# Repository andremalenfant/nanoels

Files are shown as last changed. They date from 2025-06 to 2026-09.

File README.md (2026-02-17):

Fork including:

- Touch Screen
- Upload Screen & ESP firmware from the web page
- Yellow background (a tribute to H4's design) in h5-2axis-yellow.HMI.
- Included HMI files are configured for the Nextion Enhanced 3.2" screen as it's the biggest that would fit my lathe head.
- Encoder to replace 0-9 and + - Enter, etc. to gain screen real estate (because of the smaller screen)

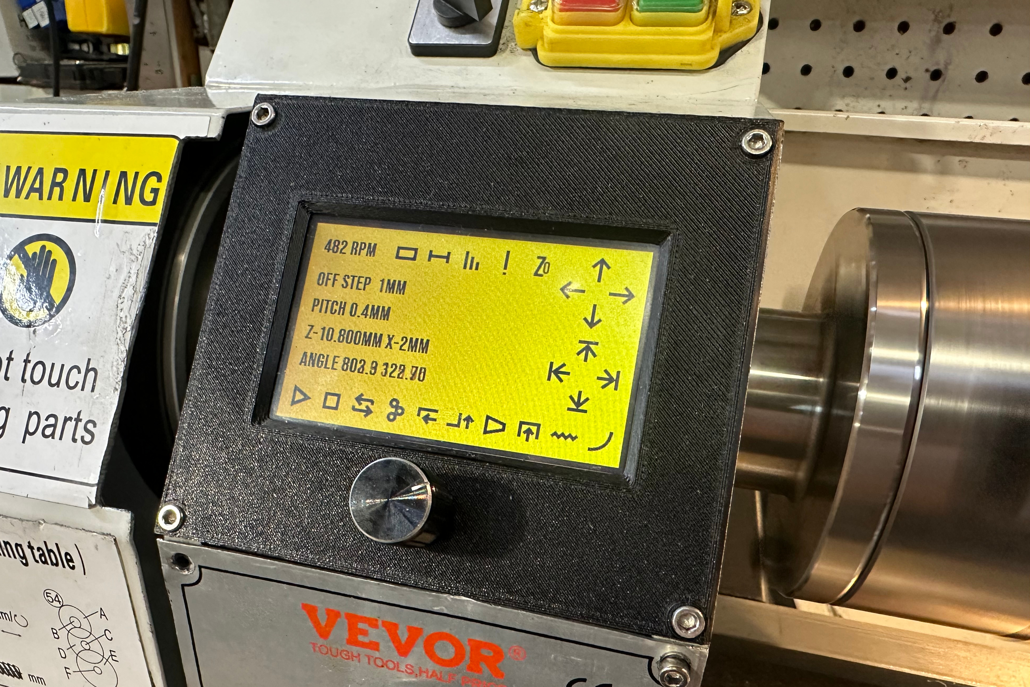
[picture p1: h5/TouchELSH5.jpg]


This software and instructions are [provided as is](LICENSE), without warranty of any kind. [🇷🇺 Перевод на русский](https://translate.google.com/translate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), [🇩🇪 deutsche Übersetzung](https://translate.google.com/translate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)

# NanoEls H5

CNC and electronic lead screw controller based on ESP32-S3 that supports up to 3 axes:

- All the features of H4
- Cheaper and much easier to make than H4
- External PS2 keyboard
- High resolution touch screen
- More ports: joystick, MPGs, scales



See [h5 folder for hardware files, software and assembly](https://github.com/kachurovskiy/nanoels/tree/main/h5).

# NanoEls H4

CNC and electronic lead screw controller based on ESP32-S3 that supports up to 4 axes:

- Automatic threads including multi-start
- Multi-pass turning, facing and cones
- Precise movements, soft limits and much more

h4-600px

See [h4 folder for hardware files, software, assembly and usage manual](https://github.com/kachurovskiy/nanoels/tree/main/h4).

## Build examples

- [fmw626](https://github.com/kachurovskiy/nanoels/discussions/123)
- [Kissys](https://github.com/kachurovskiy/nanoels/discussions/121)

# NanoEls H2

Cheap DIY Electronic Lead Screw (ELS) based on Arduino Nano for metal lathes. No more greasy gear swapping! Control your metal lathe lead screw with a few clicks.

- Set leadscrew pitch for feed or thread
- Soft limits for the carriage
- Multi-start threads in 1 start of the spindle



See [h2 folder for parts list, software, assembly and usage manual](https://github.com/kachurovskiy/nanoels/blob/main/h2/). Controller can be built from [generally available components](https://github.com/kachurovskiy/nanoels/tree/main/h2#components).

It's suggested to use STEPPERONLINE CL57T closed-loop driver with NEMA 23 3NM motor or stronger with 200 step resolution mode (full step) and a 600 PPR optical rotary encoder. [See hardware.md for more info.](hardware.md)

## Build examples

- [EdFleta](https://github.com/kachurovskiy/nanoels/discussions/87)
- [fmw626](https://github.com/kachurovskiy/nanoels/discussions/118)
- [Johannmupa](https://github.com/kachurovskiy/nanoels/discussions/89)
- [kachurovskiy](https://youtu.be/jR4tBBHSl3c?t=62)

# Contributing to the project

- Questions, problems and improvements: please start [a new GitHub Discussion](https://github.com/kachurovskiy/nanoels/discussions/new) or a new Issue
- Successful builds: please start a new GitHub Discussion with photos and comments

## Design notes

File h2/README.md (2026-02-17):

This software and instructions are provided as is, [without warranty of any kind](LICENSE).

# NanoEls H2

This is the second hardware version (hence H2) of NanoEls electronic lead screw controller. It still uses Arduino Nano
microcontroller, a [custom PCB board](https://github.com/kachurovskiy/nanoels/blob/main/h2/Gerber_PCB_NanoElsLcd_20220815.zip) you
can print cheaply on jlcpcb.com and a few widely available components allowing you to build a DIY single-axis ELS.



Features:

- Big screen
- Nice terminals
- Convenient buttons
- Disabling stepper when it's not used (less buzzing)
- Controlling left/right movement step - 1mm, 0.1mm, 0.01mm and 0.001mm
- Higher precision when turning imperial pitches
- Moving left/right while ON
- On/off switch
- Tachometer
- Multi-start threads
- Asynchronous mode
- Metric, inch and TPI support
- Quick reverse

⚠️ Due to Arduino relatively low frequency and realtime requirements (can't plan the motion ahead) H2 can only issue 2800 step impulses per second. This means that the motor can reach ~800 RPM at 200 steps per revolution or ~200 RPM at 800 steps per revolution. Make sure to use a motor with a driver that can do full steps or use the [H5 controller](https://github.com/kachurovskiy/nanoels/tree/main/h5) instead.

## Components

- Arduino Nano (mini USB style)
- 2004 LCD display
- 12 buttons 6x6mm, each 6mm tall
- 8 1kOhm resistors, one 1MOhm resistor (or similar)
- 6 M3 nylon stand-offs (12mm long) and screws
- 3 KF2EDG sockets (Curved needle, 4P, 3.5MM)
- 3 KF2EDG plugs (Plug Terminal, 4P, 3.5MM)
- MTS-102 on-off switch
- RV09 10kOhm potentiometer
- 6 M3 threaded inserts

All of this can easily be found on AliExpress, eBay or Amazon.

## Case

3D models ready for printing: [main case](https://github.com/kachurovskiy/nanoels/blob/main/h2/nanoels-lcd-case.stl),
[lid](https://github.com/kachurovskiy/nanoels/blob/main/h2/nanoels-lcd-lid.stl),
[button](https://github.com/kachurovskiy/nanoels/blob/main/h2/nanoels-lcd-button.stl). You can print it at home or e.g. at [JLCPCB](https://cart.jlcpcb.com/quote).

## Assembly

1. Check that your Arduino Nano is functional before soldering
1. Solder everything except the display onto the PCB, pay attention which side a part should be facing (up/down/left/right) and ensure Arduino pins won't be touching the display later
1. Ensure perfect soldering joints on 1kOhm resistors or the vertical row of buttons won't work well
1. Solder the display
1. Check that your board is working (connect to a PC via Arduino Nano USB port, upload code) before inserting it into the case
1. Push threaded inserts into the case using your soldering iron
1. Drill out the main case button holes using a 7mm drill and ensure the buttons are moving freely
1. Insert buttons into the case, insert PCB, screw in stand-offs (sorry, it's non-trivial), close the lid and screw it to the stand-offs

## Wiring

Starting from the top terminal:

- 5V - connect to 5V power supply positive output (usually red) through an emergency stop button
- GND - connect to 5V power supply negative output (usually black)

Encoder terminal:

- ENCA - connect to one of the encoder signal lines
- ENCB - connect to one of the encoder signal lines
- 5V - connect to encoder power-in line (usually red)
- GND - connect to encoder power-in line (usually black) and wire shielding if there's any

Stepper terminal:

- STEP - connect to stepper driver PUL-
- DIR - connect to stepper driver DIR-
- ENA - connect to stepper driver ENA-
- 5V - connect to stepper driver PUL+, DIR+, ENA+ and wire shielding if there's any

## Schematics

**WARNING:** trying to build this on a breadboard will result in [interference problems](https://github.com/kachurovskiy/nanoels/discussions/89) and will likely make the device unusable. Please use the PCB instead.



## PCB



[Gerber ZIP](https://github.com/kachurovskiy/nanoels/blob/main/h2/Gerber_PCB_NanoElsLcd_20220815.zip)

## Programming the Arduino

- Download the Arduino IDE
- Install `LiquidCrystal` and `FastGPIO` libraries via the Library Manager in the Arduino IDE
- Download [this repository](https://github.com/kachurovskiy/nanoels/archive/refs/heads/main.zip), unzip, go to `h2` directory and open `h2.ino` file in Arduino IDE
- Check the top constants (e.g. encoder steps, motor steps, display offset) and adjust if needed
- Upload the sketch to your Arduino Nano
- Spindle direction: show angle on screen using top-right button. Rotate the chuck forward manually - angle should increase. If it decreases, swap `ENC_A` and `ENC_B` values in the code, re-upload the sketch
- Motor direction: try `LEFT` and `RIGHT` buttons - if motor is moving in the wrong direction, change the value of `INVERT_STEPPER` in the code, re-upload the sketch

# Operating the ELS



## Safety

- **In case of unexpected movements use Emergency Stop button.** Ensure that your Emergency Stop button stops all motion and it can't automatically restart when Emergency Stop is lifted.
- Ensure that your machine complies with all applicable laws and regulations e.g. [Machinery Directive](https://eur-lex.europa.eu/legal-content/EN/TXT/?uri=celex%3A32006L0042) in Europe.
- Test the controller functionality before relying on it. Don't operate machinery without the necessary training and knowledge, in a hurry or when tired.

## Switching between metric and imperial

Use button that is second from the bottom in the vertical row of buttons to change the system of measurement between:

- Metric (mm)
- Inch
- TPI

It affects how the pitch and position is displayed and changes, move steps for precision moves.

## Setting pitch

Pitch is the distance that carriage will move when the spindle makes the full turn. For example, M14 thread uses 2mm pitch.

Select the desired pitch using `-` and `+` buttons. If you keep the buttons pressed, the pitch starts changing faster after a few seconds.

Use negative pitch values e.g. `-2mm` to cut left-to-right threads. Do do that, you have 2 options:

- hold the `-` button until the pitch drops below 0 to the required value
- or press the bottom-right button to toggle the pitch sign between `+` and `-`

Some inch threads require setting the micron part (3rd precision point) of the pitch, to do that click the `Step` button until you're in the `0.001mm` mode. Now clicking `-` or `+` buttons will change the pitch by a micron.

## Turning

- Set desired pitch using `-` and `+` buttons
- Turn on the lead screw using the `ON` button
- Start the lathe spindle, use `LEFT` and `RIGHT` buttons to move if needed, stop spindle when done
- Turn off the lead screw using the `ON` button

## Soft limits / automatic stops

Move the carriage using `LEFT` or `RIGHT` to the desired stop position and press `L STOP` or `R STOP` depending on which limit you'd like to set.

When both limits are set, you can:

- Use lathe forward/reverse spindle movements to move the carriage between the stops
- Use `LEFT` and `RIGHT` buttons to move the carriage within the stops

Setting only one stop is also supported. Stops aren't lost when `ON` button is clicked or pitch is changed.

## Moving the carriage

Use `LEFT` and `RIGHT` buttons to move the carriage. If stops are set, they will be respected during the movement.

When the ELS is off, carriage will move by the distance set using `Step` button but at least 1 stepper motor step.

When the ELS is ON, carriage will move in pitch increments (stay in the thread) and travel at least the distance set by `Step` button.

## Multi-start threads

Use middle button in the right-side vertical row of buttons (`Mode` button) and switch into the `MUL` mode. Use `+` and `-` buttons to increase/decrease the number of starts in your multi-start thread.

Set left and right limits. Cut thread normally and use `LEFT` or `RIGHT` buttons to move the carriage between cuts (no need to turn off the spindle). Controller automatically moves to the next start of the thread when a limit is reached.

## Asynchronous mode

Click `Mode` button until you enter the `ASY` mode. In this mode the spindle rotation is ignored and motor moves with a constant speed of 1 pitch per second when ELS is `ON`. Limits and manual movement works normally.

## Losing the thread

The spindle and stepper positions are reset to 0 `ON`, `-` or `+` buttons are pressed.

## Out-of-sync situations

It's possible for the lead screw to go out of sync with the spindle by removing the `L STOP` or `R STOP` while the carriage is standing on it. It's indicated by the `SYN` word on the display.

This situation should resolve itself once the spindle makes a full turn.

## Resetting ELS and viewing the software version

ELS remembers all the positions and ON/OFF status when powered off. Hold `ON` button for 5+ seconds to:

  - Reset stepper and spindle positions to 0
  - Resets pitch to 0
  - Removes stops
  - Removes out-of-sync state
  - Shows NanoEls version

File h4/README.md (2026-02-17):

# NanoEls H4

4-axis Electronic Lead Screw (ELS) based on ESP32-S3 for metal lathes.

h4-600px

Controller is no longer available for purchase on https://kachurovskiy.com/ but you can DIY with the hardware design files provided.

## Features

- Metric, inch and TPI support, cut any thread with utmost precision
- Controls 2 axes - lead screw (Z) and cross-slide (X)
- Manual movement of both axes: by eye, in precise steps or by a precise amount
- Disabling/enabling of stepper motors allowing to switch to manual operations in 1 click
- Soft limits allowing to cut e.g. close to the chuck
- Automatic threads: just set length, depth, pitch and number of passes
- Automatic multi-pass turning and facing
- Automatic multi-start threads
- Automatic half-spheres and ellipses
- Cone mode to cut internal or external tapers
- Cut-off mode allowing for smooth in-feed
- RPM and angle indication
- Internal/external and left-to-right versions of each automatic operation
- Backlash compensation
- Rotary encoders to move axes
- Rotary or linear 3rd axis

Advanced CNC features via [lathecode online CAD](https://github.com/kachurovskiy/lathecode):

- Running GCode over USB
- Saving GCode to device to run later

## Hardware

[Datasheet PDF](https://raw.githubusercontent.com/kachurovskiy/nanoels/main/h4/h4.pdf) contains schematic, screen, terminals and other hardware details that aren't specific do the electronic lead screw application.

See [parts.md](https://github.com/kachurovskiy/nanoels/blob/main/h4/parts.md) for Gerber, BOM, STL and other info required for DIY assembly.

See [hardware.md](https://github.com/kachurovskiy/nanoels/blob/main/hardware.md) for mounts and adapters for encoders and motors. For attaching a cross-slide motor, consider [belt-based](https://www.thingiverse.com/thing:6058899) or [gear-based](https://www.thingiverse.com/thing:4714722) NEMA 17 mounts.

## Wiring

h4-back-cropped

Encoder terminal:

- GND - connect to encoder power-in line (usually black) and wire shielding if there's any
- 5V - connect to encoder power-in line (usually red)
- ENCB - connect to one of the encoder signal lines
- ENCA - connect to one of the encoder signal lines

Z axis - stepper terminal for the main lead screw:

- 5V - connect to stepper driver PUL+, DIR+, ENA+ and wire shielding if there's any
- ENA - connect to stepper driver ENA-
- DIR - connect to stepper driver DIR-
- STEP - connect to stepper driver PUL-

X axis - stepper terminal for the cross-slide:

- 5V - connect to stepper driver PUL+, DIR+, ENA+ and wire shielding if there's any
- ENA - connect to stepper driver ENA-
- DIR - connect to stepper driver DIR-
- STEP - connect to stepper driver PUL-

Note: depending on your particular encoder, stepper driver and signal wire, H4 might not be able to provide sufficient voltage/current on the 5V output lines above due to the presence of a fuse and current-limiting resistors on the PCB. If your encoder isn't functioning or steppers are working erratically, consider supplying 5V from an external power source to the 5V lines above.

## Programming the controller

- Install the [Arduino IDE](https://docs.arduino.cc/software/ide-v2)
- Add `https://raw.githubusercontent.com/espressif/arduino-esp32/gh-pages/package_esp32_index.json` in [Preferences as "Additional board manager URLs"](https://github.com/kachurovskiy/nanoels/assets/517919/dcc023e6-20fc-4284-ba56-d466dbe4ce53)
- Install `esp32` [via Board Manager](https://github.com/kachurovskiy/nanoels/assets/517919/094d00ff-1e51-4f26-bb81-aa4ad42bde2a)
- Install Adafruit `TCA8418` library [via Library Manager](https://github.com/kachurovskiy/nanoels/assets/517919/90326e0d-6600-4b47-aa66-1177c4b9cc27)
- Download [this repository](https://github.com/kachurovskiy/nanoels/archive/refs/heads/main.zip), unzip, go to `h4` directory and open `h4.ino` file in the Arduino IDE
- Check the top constants (e.g. encoder steps, motor steps, display offset) and adjust if needed
- Select "ESP32S3 Dev Module" as device at the top, pick COM port that appears when you connect the device with a USB cable
- Upload the sketch to your H4 controller

A few things to check after upload:

- Spindle direction: show angle on screen using IconDisplay. Rotate the chuck forward manually - angle should increase. If it decreases, swap `ENCB` and `ENCA` wires in the terminal
- Motor direction: try IconArrowLeft IconArrowRight IconArrowUp IconArrowDown buttons - if motor is moving in the wrong direction, change `INVERT_Z` or `INVERT_X` in the code, re-upload the sketch (or swap the motor leads `A+` and `A-` in the stepper driver)

Troubleshooting:

- Arduino IDE doesn't detect NanoEls H4: try a different USB cable
- Not sure which COM port is NanoEls H4: unplug it, check the list of available ports in Arduino IDE, plug H4 in, see new port that appeared is H4
- `ImportError: No module named serial` error on Linux: try `sudo apt install python3-serial`

## Usage manual

**This manual corresponds to `NanoEls H4 V12`. To see your software version, hold IconStop for 5 seconds. If you have a different version - e.g. `V5`, please update to the latest one.**

### Switching between metric and imperial

Press IconMeasure to change the system of measurement between:

- Metric (mm)
- Inch
- TPI

It affects how the pitch and position is displayed and changes, move steps for precision moves.

### Setting pitch

https://github.com/kachurovskiy/nanoels/assets/517919/58da0f90-8adc-4035-a18c-198c88a73c22

Pitch is the distance that carriage will move when the spindle makes the full turn. For example, M14 thread uses 2mm pitch.

Use numpad buttons Icon0 to Icon9 to enter the pitch value. For example, pressing Icon1 Icon5 Icon0 followed by IconPlay will set the pitch to `0.15mm`, `0.15"` or `150tpi` depending on the current measurement system.

Adjust the desired pitch using IconMinus and IconPlus buttons.

Use negative pitch values e.g. `-2mm` to cut left-to-right threads. To change the pitch sign, press IconReverse.

### Setting step

https://github.com/kachurovskiy/nanoels/assets/517919/c31d04b4-958b-48af-9717-09322885c12c

Step setting is used for manual carriage moves in `off` state - i.e. when no mode is active and no thread is being cut. Current step setting is normally shown on the 1st screen line as e.g. `step 1mm` or `step 0.1"` but can be hidden if there's no space.

Pressing IconSteps cycles through the list of predefined steps:

- Metric: `1mm`, `0.1mm`, `0.01mm`
- Imperial: `0.1"`, `0.01"`, `0.001"`

Use numpad buttons Icon0 to Icon9 to enter a custom step value. Pressing IconSteps when the screen bottom line shows `Use 1.234mm?` will make the step equal to `1.234mm`.

### Zeroing the axes

Z and X position can be counted from any location you'd like. By pressing IconZ or IconX you can take the current position on the respective axis as `0`.

You can also set the `0` at a position ahead of the current position by entering the required distance using the numpad buttons Icon0 to Icon9 and then pressing IconZ or IconX.

You can set X0 on the lathe centerline by making a light cut, measuring diameter, entering it on the numpad and then pressing IconA.

### Moving left and right, in and out

https://github.com/kachurovskiy/nanoels/assets/517919/6b6dfb87-ee3a-4e2c-b272-3af0c08e09fa

Press IconArrowLeft and IconArrowRight buttons to move the carriage, IconArrowUp and IconArrowDown to move the cross-slide.

Depending on the state of the controller, pressing the move button will result in traveling the following distance:

- `off` - carriage will move by the step distance but at least 1 stepper motor step
- `ON` - carriage will move in pitch increments (stay in the thread) but at least the step distance

If step is set to `1mm` or `0.1"`, pressing and holding move buttons results in continuous movement allowing for quick tool positioning. If step is set to values other than `1mm` or `0.1"`, there's a short delay betwen steps when manual moves are triggered allowing to precisely position the tool.

Changing direction will result in automatic backlash compensation, for example with backlash `0.65mm` and step `0.1mm`, first move in the opposite direction will result in lead screw turning `0.75mm`. Tool should still only move `0.1mm` assuming backlash is uniform and is specified correclty.

When `off`, use numpad buttons Icon0 to Icon9 to enter a custom move distance. Pressing a move button when the screen bottom line shows `Use 1.234mm?` will move `1.234mm` in the corresponding direction. If there's an automatic stop limiting travel, it will move up to the limit and beep.

### Soft limits / automatic stops

https://github.com/kachurovskiy/nanoels/assets/517919/8b29bba1-941e-4e69-8598-6cb8aa0c6929

Soft limits allow to cut close to the lathe chuck, part shoulder or rear support without hitting them.

One way to set a soft limit is to move the carriage or cross-slide to the desired position and press one of the IconLimitLeft IconLimitRight IconLimitUp IconLimitDown limit buttons. Pressing the button again removes the limit regardless of the current position.

Another way to set a soft limit is to use numpad buttons Icon0 to Icon9 to enter a distance relative to the current position. Pressing a limit button when the screen bottom line shows `Use 1.234mm?` will set corresponding limit `1.234mm` away from the current position.

Soft limits are used when preparing an automatic operation like turning, facing, threading and cutting off.

### Gearbox mode / electronic lead screw

https://github.com/kachurovskiy/nanoels/assets/517919/df9fa150-0284-4aec-ab81-8e37f4a747bc

Press IconGears to switch to the gearbox mode. After turning the controller `ON` with the IconPlay button, lead screw will move the distance of 1 pitch for 1 spindle turn.

With a small pitch like `0.07mm` this mode is useful for turning - gradually taking off material from the outer diameter of the part.

With a large pitch like `0.5"` one can cut a corresponding thread. Moving with IconArrowLeft and IconArrowRight buttons is supported and does not result in losing the thread.

Direction of movement can be quickly reversed with IconReverse button which toggles the pitch sign. Negative pitch can also be used to cut left threads.

Soft limits are respected in this mode allowing to finish the cut in a precise position.

Cross-slide can be moved with manual move buttons or disabled using IconA and be operated manually.

Press IconStop to turn gearbox mode `off` and decouple lead screw movements from spindle turns.

### Automatic turning

https://github.com/kachurovskiy/nanoels/assets/517919/30d98d1e-6ddc-4f40-b637-48f76003cd33

Press IconTurning to switch to the automatic turning mode which is usually used to take large amount of material from the inside or outside diameter of the part in multiple passes.

Set the desired pitch to a suitable value e.g. `0.05mm`. Negative pitch will make turning start from the left limit, positive pitch will make it start from the right. All soft limits (left, right, up, down) must be set before the operation can be started.

Pressing IconPlay guides through remaining steps:

- Entering the numer of passes - use numpad or IconPlus and IconMinus, confirm with IconPlay
- Selecting `External` or `Internal` operation - use IconArrowLeft and IconArrowRight to change selection. Internal operations start from the IconLimitUp limit, external from the IconLimitDown limit. Confirm with IconPlay
- Confirm the final `Go?` question with IconPlay

Turn on the spindle. Operation will proceed fully automatically and the cutter will return to the starting position when done. Pitch can be adjusted on the fly using IconPlus and IconMinus.

You can skip to the next pass using IconPlay while the operation is running.

Operation can be stopped at any time by pressing IconStop or using manual move buttons.

### Automatic facing

Press IconFacing to switch to the automatic facing mode which is usually used to take large amount of material from the face of the part in 1 or more passes.

It's setup in the same way as automatic turning above. When running, passes are made along the face instead of the side of the part. Negative pitch will make facing start from the inside.

### Cone

https://github.com/kachurovskiy/nanoels/assets/517919/6dd4a5e6-12ef-45a5-a24e-4a538f206546

Press IconCone to switch to the cone mode which maintains a constant ratio of movement between the X and Z axes. Cone mode doesn't require soft limits to be set but if they are set, they are respected.

Pressing IconPlay guides through the setup:

- Enter cone ratio which is calculated as `(major_diameter - minor_diameter) / length`, see [this spreadsheet for most used values](https://docs.google.com/spreadsheets/d/1l0FUMtlWUjPywN9j94DOL84lB8dFrvdRWZIffT2NoHA/edit?usp=sharing). Confirm with IconPlay
- Select `External` or `Internal` cone - use IconArrowLeft and IconArrowRight to change selection. Confirm with IconPlay

Turn on the spindle. Pitch can be adjusted on the fly using IconPlus and IconMinus. It's convenient to cut multiple cone passes with IconReverse moving the tool in using manual move buttons.

### Automatic cut-off

https://github.com/kachurovskiy/nanoels/assets/517919/fe5245b8-4bf4-4001-8762-c786e85a2369

Press IconParting to switch to the automatic parting mode which gradually feeds the cross-slide into the part from outside or inside in one or multiple passes.

Set the desired pitch to a suitable value e.g. `0.05mm`. Negative pitch will make turning start from the inside, positive pitch will make it start from the outside. IconArrowUp and IconLimitDown soft limits must be set before the operation can be started.

Pressing IconPlay guides through remaining steps:

- Entering the numer of passes - use numpad or IconPlus and IconMinus, confirm with IconPlay
- Check that pitch corresponds to the desired direction of cutting, click IconReverse to change it
- Confirm the final `Go?` question with IconPlay

Turn on the spindle. Operation will proceed fully automatically and the cutter will return to the starting position when done. Pitch can be adjusted on the fly using IconPlus and IconMinus.

Operation can be stopped at any time by pressing IconStop or using manual move buttons.

### Automatic threading

Press IconThread to switch to the automatic threading which will cut a thread (optionally multi-start one) in multiple passes.

Set the desired pitch to a suitable value e.g. `2mm` or `20tpi`. Negative pitch will result in a left thread and will make the operation start from the left limit, positive pitch will make the operation start from the right. All soft limits (left, right, up, down) must be set before the operation can be started.

Pressing IconPlay guides through remaining steps:

- Entering the numer of passes - use numpad or IconPlus and IconMinus, confirm with IconPlay
- Selecting `External` or `Internal` operation - use IconArrowLeft and IconArrowRight to change selection. Internal operations start from the IconLimitUp limit, external from the IconLimitDown limit. For multi-start thread, press IconPlus to add more starts. Confirm with IconPlay
- Confirm the final `Go?` question with IconPlay

Turn on the spindle. Operation will proceed fully automatically and the cutter will return to the starting position when done.

You can skip to the next pass using IconPlay while the operation is running.

Operation can be stopped at any time by pressing IconStop or using manual move buttons.

### Automatic half-spheres and half-ellipses

Press IconM several times until `ELLI` is shown on screen. In this mode, cutter will form convex or concave half-ellipses in multiple passes.

Starting operation with positive pitch forms left hemisphere, with negative pitch - right hemisphere. This ensures that X backlash doesn't affect the cut.

`External` mode forms convex hemisphere (curved outward), `Internal` forms concave hemisphere (curved inward). Start and end points are the same in both cases.

Set the desired pitch to a suitable value e.g. `0.07mm`. All soft limits (left, right, up, down) must be set before the operation can be started.

Pressing IconPlay guides through remaining steps:

- Entering the numer of passes - use numpad or IconPlus and IconMinus, confirm with IconPlay
- Selecting `External` or `Internal` operation - use IconArrowLeft and IconArrowRight to change selection. Confirm with IconPlay
- Confirm the final `Go?` question with IconPlay

Turn on the spindle. Operation will proceed fully automatically and the cutter will return to the starting position when done. Adjusting the pitch on the fly is not supported.

Operation can be stopped at any time by pressing IconStop or using manual move buttons.

### Async mode

In this mode the carriage disregards spindle movements and instead moves with constant speed of `pitch` per second. When pitch is positive, `Z` axis moves to the left. When pitch is negative, `Z` axis moves to the right. If pitch is 0, `Z` axis doesn't move.

You can adjust the pitch using IconMinus or IconPlus to adjust the movement speed.

Async mode respects limits if they are set.

### GCode



**WARNING:** GCode mode ignores automatic stops. Use IconStop or emergency stop. Clicking `Stop` in the Web UI has a delay.

This mode allows to control tool movement from the PC. Programs can be generated automatically using textual part description - see [lathecode README](https://github.com/kachurovskiy/lathecode) for more info.

Before the program runs, it's critical to zero the tool:

- Set `Z=0` at the point where the left edge of the cutting tool touches the right face of the stock - e.g. by taking a light facing cut and pressing IconZ
- Set `X=0` at the point where the front edge of the cutting tool is on the centerline - e.g. take of a small amount of material from the outside diameter, enter the measured diameter using the numpad, press IconA

Before cutting your first part, zero the tool "in the air" and check that your program is doing what you expect.

Use [**lathecode online editor**](https://kachurovskiy.com/lathecode/) to define your part and run or save the GCode program to H4.

#### Saved programs

Switch to `GCODE` mode and press IconPlay.

Use IconArrowUp and IconArrowDown to select the program, IconMinus to delete the program, IconPlay to run it.

#### Technical details of the GCode mode

This section is intended for the few people sending raw serial commands to H4 - not for regular lathecode users.

Commands can be sent to device e.g. using [our Web-based GCode sender](https://kachurovskiy.github.io/nanoels/h4/sender.html) while connected over USB. The following commands are currently implemented:

- G0, G1 - linear move
- G20, G21 - inch or metric mode
- F - setting feed as mm/min or inch/min
- X, Z - single axis move
- G90, G91 - absolute or relative positioning
- G18 - ZX plane

Sample command `G1 X5 Z2 F100` will move the cutter to X=5mm, Z=2mm at 100 mm/sec in absolute metric mode.

To save a program `X0\n\Z10` under a name `Part1`, send `"Part1\nX0\n\Z10"`. To remove it, send `"Part1"`. To remove all saved programs, send `""`.

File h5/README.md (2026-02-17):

Fork including:

- Touch Screen
- Upload Screen & ESP firmware from the web page
- Yellow background (a tribute to H4's design) in h5-2axis-yellow.HMI.
- Included HMI files are configured for the Nextion Enhanced 3.2" screen as it's the biggest that would fit my lathe head.
- Encoder to replace 0-9 and + - Enter, etc. to gain screen real estate (because of the smaller screen)



# NanoEls H5

Latest version of the electronic lead screw controller for metal lathes.

h5

## Parts list

- 89€ Nextion 5 inch display [NX8048P050 011C Y](https://www.aliexpress.com/item/1005002457232503.html)
- 10€ [5V 2A non-USB power adapter](https://www.amazon.de/dp/B09KNFD38L)
- 5€ [ESP32-S3 N16R8 weld](https://www.aliexpress.com/item/1005005051294262.html)
- 3€ [SN74HCT245N](https://www.aliexpress.com/item/1005007118898020.html) - pack of 10, we only need 2
- 6€ 3 packs of [5 pairs 3.5mm terminals 4P straight](https://www.aliexpress.com/item/1005006895741900.html)
- 4€ [USB C male to female](https://www.aliexpress.com/item/1005007549815957.html)
- 5€ [custom PCB](pcb/Gerber_PCB_NanoElsH5-20241218.zip) ordered on jlcpcb.com
- [3D-printed case](case/h5case.step)
- 5x M3 bolts 5-8mm length
- Optional 23€ [PS2 mini keyboard](https://www.amazon.de/gp/product/B01MRJQVZP)
- Optional curved 4-pin header to connect display wires to the PCB

## Display options

You can use any other Nextion display model including cheaper and smaller ones without touch.

- Requires re-compiling the `h5.tft` file from the [h5.HMI](https://github.com/kachurovskiy/nanoels/blob/main/h5/screen/h5.HMI) for your display
- Needs custom 3D-printed case since `case/h5case.step` will no longer fit

## Ordering PCB

1. Go to https://cart.jlcpcb.com/quote, click "Add gerber file"
2. Use Gerber ZIP file supplied in https://github.com/kachurovskiy/nanoels/tree/main/h5/pcb/
3. Select `LeadFree HASL` and `Global Standard Direct Line` shipping
4. Should cost 5€ and arrive within 2 weeks

## Schematics and PCB component placement

schematics



## Assembly instructions

NOTE: throughout the assembly make sure to avoid static electricity accumulation on your body by wearing suitable clothes and shoes, not using chairs known to cause ESD. Touch any grounded metal device housing to check.



1. Check that ESP32 board is working by uploading [h5.ino](h5.ino) onto it using Arduino IDE. See `Programming the controller` section below for more info.
2. Solder ESP32, 2x SN74HCT245N and optional curved 4-pin header onto the PCB. **Triple check the side and orientation of each piece before soldering.**
3. Insert USB extension into the COM port
4. Separate all terminals into 2 pieces. Insert female terminals into the 3D-printed housing. Place the PCB on top and secure it with 4 M3 bolts. Secure the other end of the USB cable in the access hole with an M3 bolt.
5. Solder 15 terminals to the PCB while everything is positioned in the case.
6. Remove screen back cover. Attach the included 4-lead wire to the screen and to the PCB - each `RX` should be attached to `TX` on the other side.
7. Bolt the case and screen together using the bolts that used to hold the back cover.
8. Use empty MicroSD card 32 GB or smaller formatted as FAT32. Copy [h5.tft](screen/h5.tft) to the card, insert into the screen. Connect 5V power supply to the POWER terminal, wait for screen to report that flashing has finished. Disconnect the power, remove the card.
9. Cut the keyboard cord to the suitable length, find which color corresponds to which line in your particular keyboard [using the port pinout](https://en.wikipedia.org/wiki/PS/2_port) and multimeter continuity tester.
10. Supply up to 2A of power to the `POWER` terminal. You can flash the ESP32 via the USB but 0.5A provided by standard USB is not enough to start the screen.

## Rear label

Print [h5.pdf](case/h5.pdf) on a normal printer as A4 at 19% scale, cut out and glue to the back of the case using e.g. double-sided tape.

If you want, you can modify the label by editing [h5.fig](case/h5.fig) file on figma.com and export a new PDF for printing.

## Wiring

ENCODER terminal:

- 5V - connect to encoder power-in line (usually red)
- GND - connect to encoder power-in line (usually black) and wire shielding if there's any
- ENCB - connect to one of the encoder signal lines
- ENCA - connect to one of the encoder signal lines

Z and X axes - stepper terminal for the lead screws:

- 5V - connect to stepper driver PUL+, DIR+, ENA+ and wire shielding if there's any
- ENA - connect to stepper driver ENA-
- DIR - connect to stepper driver DIR-
- STEP - connect to stepper driver PUL-

Pulse motion wheels for Z and X axes (`ZPULSE`, `XPULSE`) are wired in the same manner as the encoder. For any encoder terminal, switch `A` and `B` wires to invert the encoder direction.

Scale and joystick terminals aren't used in the code yet.

## Programming the controller

- Install the [Arduino IDE](https://docs.arduino.cc/software/ide-v2)
- Add `https://raw.githubusercontent.com/espressif/arduino-esp32/gh-pages/package_esp32_index.json` in [Preferences as "Additional board manager URLs"](https://github.com/kachurovskiy/nanoels/assets/517919/dcc023e6-20fc-4284-ba56-d466dbe4ce53)
- Install `esp32` [via Board Manager](https://github.com/kachurovskiy/nanoels/assets/517919/094d00ff-1e51-4f26-bb81-aa4ad42bde2a)
- Install `PS2KeyAdvanced` and `WebSockets` via Arduino IDE Library Manager
- Download [this repository](https://github.com/kachurovskiy/nanoels/archive/refs/heads/main.zip), unzip, go to `h5` directory and open `h5.ino` file in the Arduino IDE
- Check the top constants (e.g. encoder steps, motor steps, display offset) and adjust if needed
- Select "ESP32S3 Dev Module" as device at the top, pick COM port that appears when you connect the device with a USB cable
- Upload the sketch to your H5 controller

A few things to check after upload:

- Spindle direction: rotate the chuck forward manually - angle on screen should increase. If it decreases, swap `B` and `A` wires in the terminal
- Motor direction: try moving motors using keyboard arrows - if motor is moving in the wrong direction, change `INVERT_Z` or `INVERT_X` in the code, re-upload the sketch (or swap the motor leads `A+` and `A-` in the stepper driver if it's open loop)

Troubleshooting:

- Arduino IDE doesn't detect NanoEls H5: try a different USB cable
- Arduino IDE fails to upload the sketch: make sure you plugged the extension into the `COM` port, **not** the `USB` port on the ESP32
- Not sure which COM port is NanoEls H5: unplug it, check the list of available ports in Arduino IDE, plug H5 in, see new port that appeared is H5
- `ImportError: No module named serial` error on Linux: try `sudo apt install python3-serial`

## Mounting options

On the back of the case there are 2 holes for M5 threaded inserts 130mm on center.

## GCode over WiFi for complex parts

Specify your WiFi network name and password in https://github.com/kachurovskiy/nanoels/blob/main/h5/h5.ino#L45-L46 and NanoEls will show the IP address on screen once it connects to the network. Enter that address in the browser to see the Web UI. It can be used to save GCode files onto controller and run them later at the machine in the GCODE mode.

To generate GCode for your parts, upload STL model of your part to https://kachurovskiy.com/lathecode/ and specify parameters like stock diameter and tool used.

Handwheels and limits have no effect when GCODE is running.



## Custom keyboard mapping

Use [`#define B_...`](https://github.com/kachurovskiy/nanoels/blob/main/h5/h5.ino#L124) constants to adjust key mapping, uncomment [a line](https://github.com/kachurovskiy/nanoels/blob/main/h5/h5.ino#L3001) in `void processKeypadEvent()` function to see on Nextion which key code your keyboard sends for any given key.

## Usage manual

Controller can be controlled via touchscreen and/or keyboard. Keyboard is optional but it's much nicer to use mechanical buttons for manual moves and not worrying about accidentally pressing a nearby button on the touchscreen.

### Touchscreen

If descriptions of the buttons below are unclear, don't worry, skip this section and read the rest of the manual, that should clarify things.

h5v11screen

Top line:

- `bStatus` turns the controlled off - stops the ongoing operation or manual move, resets spindle angle and turns to 0
- `bMode` turns the controlled off and changes the mode
- `mMultistart` increases the amounts of starts by 1 when pressed in short intervals, sets amount of starts to 1 if pressed after a pause
- `tPitch` reverses the pitch - makes it positive if it's negative, makes it negative if it's positive. Reversing makes the controller "loose the thread" so don't use it for returning back for another threading pass.
- `bMeasure` changes measuring system between metric, imperial and tpi
- `mPlus` increments the pitch or number of passes in a multi-pass operation
- `mMinus` decrements the pitch or number of passes in a multi-pass operation

Middle line:

- `tStepVal` toggles between different step sizes used in manual moves
- `tRPMVal` shows current rotations per minute of the spindle
- `tTurnsVal` shows the number of full turns performed by the spindle since the last off/stop command
- `tAngleVal` shows the current angle of the spindle

X axis group:

- `mXUp` and `tXUp` clear the up limit if it's set, sets the limit in the current `X` position if it's not set
- `bX` enables or disables the axis. When pressed with active numpad input, considers the input as measured diameter of the part at current cutter position and sets `X` zero to negative half of the given diameter.
- `tX` take current `X` position as zero
- `mXDown` and `tXDown` clear the down limit if it's set, sets the limit in the current `X` position if it's not set
- `m0` moves cross-slide forward
- `m1` moves cross-slide back

Y axis group:

- `mYUp` and `tYUp` clear the positive `Y` limit if it's set, sets the limit in the current negative `Y` position if it's not set
- `bY` enables or disables the axis
- `tY` take current `Y` position as zero
- `mYDown` and `tYDown` clear the down limit if it's set, sets the limit in the current `Y` position if it's not set
- `m2` moves `Y` axis forward
- `m5` moves `Y` axis back

Z axis group:

- `m3` and `tZLeft` clear the left limit if it's set, sets the limit in the current `Z` position if it's not set
- `bZ` enables or disables the axis
- `tZ` take current `Z` position as zero
- `m4` and `tZRight` clear the right limit if it's set, sets the limit in the current `Z` position if it's not set
- `m6` moves the carriage left
- `m7` moves the carriage right

Lower part of the screen:

- `t3` shows diameter, current WiFi status, pending numpad value or mode configuration prompt
- `mStop` turns the controlled off
- `bD0` to `bD9` append a number at end of the numpad input
- `mBack` works as backspace - deletes the last entered number
- `mPlay` starts the current mode or proceeds to the next step of mode configuration

### Keyboard

- ⌨️`Left`, ⌨️`up`, ⌨️`down`, ⌨️`right` arrows control the manual movement
- ⌨️`Plus` / ⌨️`minus` control the pitch
- ⌨️`Enter` turns on the current mode
- ⌨️`Esc` is stop
- ⌨️`A` / ⌨️`W` / ⌨️`D` / ⌨️`S` control limits
- ⌨️`Win` controls angle / rpm display / WiFi status
- ⌨️`Tilda` / ⌨️`backtick` (key under ESC) controls step
- ⌨️`M` changes metric / inch / tpi
- ⌨️`R` for reverse
- Top row numbers ⌨️`0`-⌨️`9` work as number input
- ⌨️`Backspace` removes last number
- Modes:
  - ⌨️`F1`: gearbox
  - ⌨️`F2`: turning
  - ⌨️`F3`: facing
  - ⌨️`F4`: cone
  - ⌨️`F5`: parting
  - ⌨️`F6`: threading
  - ⌨️`F7`: async
  - ⌨️`F8`: ellipse
  - ⌨️`F9`: gcode
  - ⌨️`F10`: y axis (if configured)
- ⌨️`X` zeroes X axis
- ⌨️`Z` zeroes Z axis
- ⌨️`C` disables / enables X axis
- ⌨️`Q` disables / enables Z axis
- ⌨️`O` pressed while a number is entered zeroes X from diameter

### Convention for referring to screen or keyboard buttons in this manual

Text like 🖥️`bMeasure` refers to looking at or pressing on the corresponding area of the screen, in this case green "IN" rectangle in the upper-right part of it.

Text like ⌨️`M` refers to pressing the corresponding letter on the keyboard, in this case letter M.

Dash between symbols refers to all the buttons between the 2 mentioned buttons e.g. ⌨️`1`-`0` means `1`, `2`, `3`, `4`, `5`, `6`, `7`, `8`, `9`, `0` keys on the keyboard.

Slash between symbols refers to either one of the symbols e.g. ⌨️`+`/`-` means "pressing plus or minus key on the keyboard".

### Switching between metric and imperial

Press 🖥️`bMeasure` or ⌨️`M`  to change the system of measurement between:

- Metric (mm)
- Inch
- TPI

It affects how the pitch and position is displayed and changes, move steps for precision moves.

### Setting pitch

Pitch is the distance that carriage will move when the spindle makes the full turn. For example, M14 thread uses 2mm pitch.

Use numpad buttons 🖥️`bD0`-`bD9` or ⌨️`1`-`0` to enter the pitch value, 🖥️`mPlay` or ⌨️`Enter` to accept it.

Adjust the desired pitch using 🖥️`mPlus`/`mMinus` or ⌨️`+`/`-`.

Use negative pitch values e.g. `-2mm` to cut left-to-right threads. To change the pitch sign, press 🖥️`tPitch` or ⌨️`R`.

### Setting step

Step setting is used for manual carriage moves in `off` state - i.e. when no mode is active and no thread is being cut. Current step setting is normally shown in 🖥️`tStepVal`.

Pressing 🖥️`tStepVal` or ⌨️`Key under ESC` cycles through the list of predefined steps:

- Metric: `1mm`, `0.1mm`, `0.01mm`
- Imperial: `0.1"`, `0.01"`, `0.001"`

Use 🖥️`bD0`-`bD9` or ⌨️`1`-`0` to enter a custom step value. Pressing 🖥️`tStepVal` or ⌨️`Key under ESC` when the screen bottom line shows `Use 1.234mm?` will make the step equal to `1.234mm`.

### Zeroing the axes

Z and X position can be counted from any location you'd like. By pressing e.g. 🖥️`tZ` or ⌨️`Z` you can take the current position on the respective axis as `0`.

You can also set the `0` at a position ahead of the current position by entering the required distance using the numpad buttons 🖥️`bD0`-`bD9` or ⌨️`1`-`0` and then pressing 🖥️`tZ` or ⌨️`Z`.

You can set X0 on the lathe centerline by making a light cut, measuring diameter, entering it on the numpad and then pressing 🖥️`BX` or ⌨️`O`.

### Moving left and right, in and out

Press 🖥️`m6`/`m7` / ⌨️`Left`/`Right` buttons to move the carriage, 🖥️`m0`/`m1` / ⌨️`Up`/`Down` to move the cross-slide.

Depending on the state of the controller, pressing the move button will result in traveling the following distance:

- `off` - carriage will move by the step distance but at least 1 stepper motor step
- `ON` - carriage will move in pitch increments (stay in the thread) but at least the step distance

If step is set to `1mm` or `0.1"`, pressing and holding move buttons results in continuous movement allowing for quick tool positioning. If step is set to values other than `1mm` or `0.1"`, there's a short delay betwen steps when manual moves are triggered allowing to precisely position the tool.

Changing direction will result in automatic backlash compensation, for example with backlash `0.65mm` and step `0.1mm`, first move in the opposite direction will result in lead screw turning `0.75mm`. Tool should still only move `0.1mm` assuming backlash is uniform and is specified correclty.

When `off`, use numpad buttons 🖥️`bD0`-`bD9` / ⌨️`1`-`0` to enter a custom move distance. Pressing a move button when the screen bottom line shows `Use 1.234mm?` will move `1.234mm` in the corresponding direction. If there's an automatic stop limiting travel, it will move up to the limit and beep.

### Soft limits / automatic stops

Soft limits allow to cut close to the lathe chuck, part shoulder or rear support without hitting them.

One way to set a soft limit is to move the carriage or cross-slide to the desired position and press one of the 🖥️`tZLeft`/`tZRight`/`tXUp`/`tXDown` / ⌨️`A`/`W`/`D`/`S` limit buttons. Pressing the button again removes the limit regardless of the current position.

Another way to set a soft limit is to use numpad buttons 🖥️`bD0`-`bD9` / ⌨️`1`-`0` to enter a distance relative to the current position. Pressing a limit button when the screen bottom line shows `Use 1.234mm?` will set corresponding limit `1.234mm` away from the current position.

Soft limits are used when preparing an automatic operation like turning, facing, threading and cutting off.

### Gearbox mode / electronic lead screw

Press 🖥️`bMode` to switch to the gearbox mode. After turning the controller `ON` with the 🖥️`mPlay` / ⌨️`Enter` button, lead screw will move the distance of 1 pitch for 1 spindle turn.

With a small pitch like `0.07mm` this mode is useful for turning - gradually taking off material from the outer diameter of the part.

With a large pitch like `0.5"` one can cut a corresponding thread. Moving with 🖥️`m6` and 🖥️`m7` buttons is supported and does not result in losing the thread.

Direction of movement can be quickly reversed with 🖥️`tPitch` / ⌨️`R` button which toggles the pitch sign. Negative pitch can also be used to cut left threads.

Soft limits are respected in this mode allowing to finish the cut in a precise position.

Cross-slide can be moved with manual move buttons or disabled using 🖥️`bX` / ⌨️`C` and be operated manually.

Press 🖥️`mStop` / ⌨️`Esc` to turn gearbox mode `off` and decouple lead screw movements from spindle turns.

### Automatic turning

Press 🖥️`bMode` to switch to the automatic turning mode which is usually used to take large amount of material from the inside or outside diameter of the part in multiple passes.

Set the desired pitch to a suitable value e.g. `0.05mm`. Negative pitch will make turning start from the left limit, positive pitch will make it start from the right. All soft limits (left, right, up, down) must be set before the operation can be started.

Pressing 🖥️`mPlay` / ⌨️`Enter` guides through remaining steps:

- Entering the numer of passes - use numpad or 🖥️`mPlus`/`mMinus` / ⌨️`+`/`-`, confirm with 🖥️`mPlay` / ⌨️`Enter`
- Selecting `External` or `Internal` operation - use 🖥️`m6` and 🖥️`m7` to change selection. Internal operations start from the 🖥️`tXUp` limit, external from the 🖥️`tXDown` limit. Confirm with 🖥️`mPlay` / ⌨️`Enter`
- Confirm the final `Go?` question with 🖥️`mPlay` / ⌨️`Enter`

Turn on the spindle. Operation will proceed fully automatically and the cutter will return to the starting position when done. Pitch can be adjusted on the fly using 🖥️`mPlus`/`mMinus` / ⌨️`+`/`-`.

You can skip to the next pass using 🖥️`mPlay` / ⌨️`Enter` while the operation is running.

Operation can be stopped at any time by pressing 🖥️`mStop` / ⌨️`Esc` or using manual move buttons.

In previous versions cross-slide would pull back all the way between the passes, starting from H5V12 we only pull back by a small safe distance.

Handwheels are ignored when this mode is on.

### Automatic facing

Press 🖥️`bMode` to switch to the automatic facing mode which is usually used to take large amount of material from the face of the part in 1 or more passes.

It's setup in the same way as automatic turning above. When running, passes are made along the face instead of the side of the part. Negative pitch will make facing start from the inside.

### Cone

Press 🖥️`bMode` to switch to the cone mode which maintains a constant ratio of movement between the X and Z axes. Cone mode doesn't require soft limits to be set but if they are set, they are respected.

Pressing 🖥️`mPlay` / ⌨️`Enter` guides through the setup:

- Enter cone ratio which is calculated as `(major_diameter - minor_diameter) / length`, see [this spreadsheet for most used values](https://docs.google.com/spreadsheets/d/1l0FUMtlWUjPywN9j94DOL84lB8dFrvdRWZIffT2NoHA/edit?usp=sharing). Confirm with 🖥️`mPlay` / ⌨️`Enter`
- Select `External` or `Internal` cone - use 🖥️`m6` and 🖥️`m7` to change selection. Confirm with 🖥️`mPlay` / ⌨️`Enter`

Turn on the spindle. Pitch can be adjusted on the fly using 🖥️`mPlus`/`mMinus` / ⌨️`+`/`-`. It's convenient to cut multiple cone passes with 🖥️`tPitch` / ⌨️`R` moving the tool in using manual move buttons.

### Automatic cut-off

Press 🖥️`bMode` to switch to the automatic parting mode which gradually feeds the cross-slide into the part from outside or inside in one or multiple passes.

Set the desired pitch to a suitable value e.g. `0.05mm`. Negative pitch will make turning start from the inside, positive pitch will make it start from the outside. 🖥️`tXUp` and 🖥️`tXDown` soft limits must be set before the operation can be started.

Pressing 🖥️`mPlay` / ⌨️`Enter` guides through remaining steps:

- Entering the numer of passes - use numpad or 🖥️`mPlus`/`mMinus` / ⌨️`+`/`-`, confirm with 🖥️`mPlay` / ⌨️`Enter`
- Check that pitch corresponds to the desired direction of cutting, click 🖥️`tPitch` / ⌨️`R` to change it
- Confirm the final `Go?` question with 🖥️`mPlay` / ⌨️`Enter`

Turn on the spindle. Operation will proceed fully automatically and the cutter will return to the starting position when done. Pitch can be adjusted on the fly using 🖥️`mPlus`/`mMinus` / ⌨️`+`/`-`.

Operation can be stopped at any time by pressing 🖥️`mStop` / ⌨️`Esc` or using manual move buttons.

Handwheels are ignored when this mode is on.

### Automatic threading

Press 🖥️`bMode` to switch to the automatic threading which will cut a thread (optionally multi-start one) in multiple passes.

First passes are larger than average, final passes are shallower.

Set the desired pitch to a suitable value e.g. `2mm` or `20tpi`. Negative pitch will result in a left thread and will make the operation start from the left limit, positive pitch will make the operation start from the right. All soft limits (left, right, up, down) must be set before the operation can be started.

Pressing 🖥️`mPlay` / ⌨️`Enter` guides through remaining steps:

- Entering the numer of passes - use numpad or 🖥️`mPlus`/`mMinus` / ⌨️`+`/`-`, confirm with 🖥️`mPlay` / ⌨️`Enter`
- Selecting `External` or `Internal` operation - use 🖥️`m6`/`m7` or ⌨️`Left`/`Right` to change selection. Internal operations start from the 🖥️`tXUp` limit, external from the 🖥️`tXDown` limit. For multi-start thread, press 🖥️`mPlus` to add more starts. Confirm with 🖥️`mPlay` / ⌨️`Enter`
- Enter optional cone ratio on the numpad. Confirm with 🖥️`mPlay` / ⌨️`Enter`
- Confirm the final `Go?` question with 🖥️`mPlay` / ⌨️`Enter`

Turn on the spindle. Operation will proceed fully automatically and the cutter will return to the starting position when done.

You can skip to the next pass using 🖥️`mPlay` / ⌨️`Enter` while the operation is running.

Operation can be stopped at any time by pressing 🖥️`mStop` / ⌨️`Esc` or using manual move buttons.

### Automatic half-spheres and half-ellipses

Press 🖥️`bMode` several times until `ELLI` is shown on screen. In this mode, cutter will form convex or concave half-ellipses in multiple passes.

Starting operation with positive pitch forms left hemisphere, with negative pitch - right hemisphere. This ensures that X backlash doesn't affect the cut.

`External` mode forms convex hemisphere (curved outward), `Internal` forms concave hemisphere (curved inward). Start and end points are the same in both cases.

Set the desired pitch to a suitable value e.g. `0.07mm`. All soft limits (left, right, up, down) must be set before the operation can be started.

Pressing 🖥️`mPlay` / ⌨️`Enter` guides through remaining steps:

- Entering the numer of passes - use numpad or 🖥️`mPlus`/`mMinus` / ⌨️`+`/`-`, confirm with 🖥️`mPlay` / ⌨️`Enter`
- Selecting `External` or `Internal` operation - use 🖥️`m6`/`m7` / ⌨️`Left`/`Right` to change selection. Confirm with 🖥️`mPlay` / ⌨️`Enter`
- Confirm the final `Go?` question with 🖥️`mPlay` / ⌨️`Enter`

Turn on the spindle. Operation will proceed fully automatically and the cutter will return to the starting position when done. Adjusting the pitch on the fly is not supported.

Operation can be stopped at any time by pressing 🖥️`mStop` / ⌨️`Esc` or using manual move buttons.

Handwheels are ignored when this mode is on.

### Async mode

In this mode the carriage disregards spindle movements and instead moves with constant speed of `pitch` per second. When pitch is positive, `Z` axis moves to the left. When pitch is negative, `Z` axis moves to the right. If pitch is 0, `Z` axis doesn't move.

You can adjust the pitch using 🖥️`mMinus`/`mPlus` to adjust the movement speed.

Async mode respects limits if they are set.

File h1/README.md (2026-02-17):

**This software and instructions are provided as is, without warranty of any kind. This is a hobby project. Using this might damage your equipment, cause injury or death. Use at your own risk.**

# NanoEls H1

**This page is provided for people who have already built or have already started building H1 version of the ELS. If you're just starting, use the new and improved [H2 version](https://github.com/kachurovskiy/nanoels/tree/main/h2).**

Cheap DIY Electronic Lead Screw (ELS) based on Arduino Nano for metal lathes.

NanoEls explosion diagram

# Features

- Positive and negative screw pitches
  - From -10mm to 10mm
  - Resolution 0.01mm
- Automatic lead screw stops
- Independent carriage moves without losing the thread
- Lead screw position indication
- Spindle angle indication

# Hardware overview

- 5 plastic 3D-printed parts (gears, mounts)
- Uses readily available hardware
  - 46€ Nema 23 stepper and driver (50% more for closed loop)
  - 16€ 48V 5A power supply
  - 9€ printed curcuit board (PCB)
  - 9€ rotary encoder
  - 3€ Arduino Nano
  - 3€ push buttons
  - 2€ OLED display
  - 5V power supply e.g. an old phone charger
  - 8 bolts, 2 nuts, 2 washers and a few wires
  - Optionally, two `2kOhm` resistors
- Does not require metalworking
- Does not require drilling holes in the lathe

# Other hardware required

- Soldering iron, solder
- Hex and screwdrivers
- Soft hammer or a woodworking clamp
- 50T metal gear that your lathe came with
- Grease for the gears

# Build examples

- [bestbean](https://github.com/kachurovskiy/nanoels/discussions/109)
- [Dididu12](https://github.com/kachurovskiy/nanoels/discussions/40#discussioncomment-2019521)
- [Hedning003](https://github.com/kachurovskiy/nanoels/discussions/16)
- [HW61](https://github.com/kachurovskiy/nanoels/discussions/43)
- [kachurovskiy](https://www.youtube.com/watch?v=9uTdDk2EqG4?t=272)
- [mockendon](https://github.com/kachurovskiy/nanoels/discussions/32)
- [Sonny Madlangbayan](https://www.youtube.com/watch?v=qiPQUa50Uog)
- [wberggren](https://github.com/kachurovskiy/nanoels/discussions/13)
- [WillieJilesen](https://github.com/kachurovskiy/nanoels/discussions/39)
- [zabu83](https://github.com/kachurovskiy/nanoels/discussions/11)

# Limitations

- PLA plastic gears and mounts shouldn't heat up or they will deform and disconnect. Stepper can heat up quite a bit during continuous operation. Depending on the stepper driver current, the limit seems to be ~50% duty cycle with 10min operation / 10min cooldown. For higher duty cycle something like metal HTD 5M gears, belt and a metal stepper mount would be required. Another option is using PETG or ABS.
- Nema 23 stepper usable maximum is ~600 RPM, here a 1:1 stepper to leadscrew ratio is used. In practice this means that cutting e.g. 2mm thread with a 2mm leadscrew spindle top speed should stay under 600 RPM.
  - Cheap brand-less drivers are worse at handling high RPM
  - NanoEls would take the stepper at 1000 RPM and higher but it likely won't have much torque at that point
  - This can be mitigated to some extent by using e.g. 40 tooth gear on the leadscrew and 60 tooth gear on the motor at the expense of the maximum leadsrew torque
- Lead screw position only equals the carriage position if the backlash was taken out before the measurement started. Changing the direction introduces the backlash again.

# Big display

NanoEls also supports LCD2004 displays [such as this one (4€)](https://www.aliexpress.com/item/4001135515638.html). Those are 20-char, 4-line with 5mm tall letters comparing to 2.5mm tall letters on an OLED display. Full update takes `57ms` on an LCD comparing to `46ms` on OLED. The backlight could be a bit uncofortable for the eyes, see [a visual comparison](https://imgur.com/a/TbHg9Y3).

If you're using LCD2004, uncomment the line `#define LCD`, install the library `LiquidCrystal I2C` from [Frank de Brabander](https://github.com/fdebrabander) via the Library Manager and re-upload the sketch.

# Instructions

We've tried to simplify the process as much as possible but building NanoEls is still going to take considerable time and effort, basic mechanical and electrical knowledge.

You might need to design your own mounts and gears if the ones we have don't fit. If you need help designing a 3D printed part, please open a GitHub Issue with exact dimensions of the part that you need.

## Parts

See https://github.com/kachurovskiy/nanoels/blob/main/hardware.md for encoder, motor, gearing and mounting info.

### Arduino Nano

The code was tested using an Arduino Nano V3 clone.

### OLED display

SSD1306 monochrome 4-pin I2C OLED 128x64 display. **Warning:** make sure that your OLED has legs in the following order to work on the PCB - GND VCC SCL SDA.

### Buttons

Using 6x6x13mm switches. 13mm is the optimal height for the provided case, if you're using a different case, desired height might be different. AliExpress has very convenient 200 button sets of different height for a few euros.

6x6 buttons can be too small for fingers to comfortably click, consider buying caps to put on them, keywords for AliExpress are "switch push button hat 6mm".

### 5V power supply

Arduino Nano doesn't draw much current so a 5V 0.5A phone charger would work.

### PCB

NanoEls H1 PCB

[Gerber ZIP for production](https://github.com/kachurovskiy/nanoels/blob/main/h1/pcb/nanoels-pcb-h1.zip)

It's a 70mm by 90mm board with holes for M3 mounting bolts, 1.6mm thick. You will need clearance above, below and on the sides of the board for the through-hole components, their pins (legs) and wires coming into the PCB.

PCB is best placed away from the electromagnetic noise sources such as lathe motor wires. Grounded metal housing is ideal.

**Some PCB production techniques use lead and other nasty stuff. Order at your own risk and dispose properly.**

Ordering it from JLCPCB takes just a few clicks - upload the ZIP file, use all default settings, choose shipping and checkout.

### 3D-printed parts

#### Case

Case

[STL part 1](https://github.com/kachurovskiy/nanoels/raw/main/h1/case/nanoels-box-part1.stl) and [part 2](https://github.com/kachurovskiy/nanoels/raw/main/h1/case/nanoels-box-part2.stl)

Case size is 102x82x27mm. PCB is mounted onto the case with 4 M3 bolts.

## Assembly

**Working with electrical wiring is dangerous, unplug the lathe. Proceed at your own risk.**

Connect the 24V and 5V power supplies to the lathe power so that the lathe on/off and safety switches cut off the power for the ELS too.

Test Arduino Nano **before** soldering it on, unsoldering it without a desoldering station is very hard.

Don't solder the Arduino upside-down or rotated 180 degrees, check the white outlines on the board.

Carefully solder 10 buttons (6X6X11 switches to fit the provided case), OLED 128x64 4-pin display and an Arduino Nano onto it. Plug USB into Arduino to test - display and buttons shoulad already work.

It's important that buttons are soldered vertically or the result won't fit into a case. To achieve this, solder only 2 diagonal legs for each button first while pressing on the button firmly. Then check all buttons for verticalness, at this point it's easy to correct the angle by pressing on the button and re-heating one of the legs. Once satisfied, proceed to solder all the remaining legs. 

Assembly

Solder 5V/GND wires to the PCB.

Solder encoder and stepper driver wires to the PCB according to the input/output labels on the PCB.

PCB wiring

**Important: there can be a metal mesh under the insulation around your wires, it's shielding, don't just cut it off. Solder it to ground (GND), together with the black ground cable.**

Screw terminals are designed to be soldered on the bottom side of the PCB.

Optinally solder two 2kOhm pull-up resistors. They aren't strictly needed but will improve the stability of the optical encoder readings.

## Programming the Arduino

- Download the Arduino IDE
- Install `Adafruit_SSD1306` and `FastGPIO` libraries via the Library Manager in the Arduino IDE
- Download and open [NanoEls.ino](https://github.com/kachurovskiy/nanoels/raw/main/h1/NanoEls.ino)
- Check the top constants (e.g. encoder steps, motor steps, display offset) and adjust if needed
- Upload the sketch to your Arduino Nano
- Swap D2 and D3 pins in the code if carriage direction is inverted, re-upload

# Operating the ELS

## Safety

- Make sure that stepper motor and ELS are turned off using the lathe emergency power off switch
- Test the automatic stop and other ELS functionality before relying on it
- **In case of unexpected movements, disengage the half-nut or use the emergency power off switch**

## Turning

- Select the desired pitch using `-` and `+` buttons or `0.10mm`, `1mm` and `2mm` shortcut buttons in the top row
- Turn on the lead screw using the `ON` button
- Start the lathe spindle
- Stop the lathe spindle when done
- Turn off the lead screw using the `ON` button

## Automatic stops

- Move the carriage with the help of ELS to the desired stop position
- Set the stop using e.g. `L STOP` button
- Hold `RIGHT` to move to another stop position and press `R STOP`

Now you can:

- Use lathe forward/reverse spindle movements to move the carriage between the stops
- Use `LEFT` and `RIGHT` buttons to move the carriage ~1mm (possibly more when required to stay on the thread) within the stops in either direction when spindle is not turning

Setting only one stop is also supported. Stops aren't lost when `ON` button is clicked or pitch is changed.

## Carriage movements

- Make sure the cutting tool is not going to contact the material and there's room to move the carriage physically
- Use `LEFT` and `RIGHT` buttons to move the carriage ~1mm (possibly more or less when required to stay on the thread) when spindle is not turning
- If stops are set, they will be respected

Using `LEFT` and `RIGHT` buttons is not supported when the spindle is turning and ELS is on.

## Losing the thread

The spindle and stepper positions are reset to 0 every time one of the following happens:

- `ON` button is pressed (including long press for reset)
- Pitch is changed e.g. by pressing `-` or `+`
- Stepper is not in the desired position when ELS is powered up
  - Results in `LTW` lost thread warning
  - Might happen if ELS was abruptly shutdown

Thread is **not** lost when ELS is simply powered off.

## Out-of-sync situations

It's possible for the lead screw to go out of sync with the spindle by removing the `L STOP` or `R STOP` while the carriage is standing on it. It's indicated by the `SYN` word on the display.

This situation should resolve itself once the spindle makes a full turn.

## Resetting ELS and viewing the software version

ELS remembers all the positions and ON/OFF status when powered off.

- Hold `ON` button for 6 seconds
  - Reset stepper and spindle positions to 0
  - Resets pitch to 0
  - Removes stops
  - Removes out-of-sync state
  - Shows NanoEls version

# Troubleshooting

## My stepper is skipping steps

1. Check that `ENCODER_STEPS`, `MOTOR_STEPS` and `LEAD_SCREW_HMM` parameters you used match your hardware. E.g. if you tell ELS that `MOTOR_STEPS` is 400 but your actual driver is set to 200, ELS will try to move the stepper too fast and it will stall.
2. Check the mechanical connection between the stepper and the lead screw, try rotating the stepper by hand when lathe is OFF. It shouldn't be too hard to turn. If you're using gears, ensure they're turning freely, not jamming and have a tiny bit of backlash. If you're using a belt, make sure it's not overtightened.
3. Try using higher voltage, within limits of your stepper and driver. For NEMA 23, best performance is achieved at 48V but the driver has to support it.
4. Try increasing the current on your driver, within the limits of your stepper.
5. If you have a cheap brand-less driver, consider getting a higher quality driver.
6. For an immediate fix, change the acceleration (line 23) PULSE_DELTA_US from `7` to `2`, PULSE_MIN_US (line 21) from `500` to e.g. `700`.
7. Consider using a sufficently strong closed-loop stepper instead. I didn't try them myself but there are some high-rated closed loop stepper-driver sets on AliExpress for 69€.

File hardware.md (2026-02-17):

**This software and instructions are provided as is, without warranty of any kind. This is a hobby project. Using this might damage your equipment, cause injury or death. Use at your own risk.**

# Mechanical part of the ELS



Any electronic lead screw requires connecting an encoder to the lathe spindle and motor to the leadscrew.
This page provides some general guidance but every lathe is different, start a new [discussion](https://github.com/kachurovskiy/nanoels/discussions) if you have questions.

# Encoder

Tested with the [following 600 steps encoder](https://www.aliexpress.com/item/4001142743940.html). They are available on eBay/AliExpress as "optical rotary encoder".

## Encoder base

Encoder base

[STEP file for 3D printing](https://github.com/kachurovskiy/nanoels/raw/main/h1/encoder/EncoderMount38.4mm-Body.step)

Attached using 2x M4 bolts to the side of the headstock. Using an M4 set screw is optional.

Alternative encoder base allowing for a thicker cable: https://www.thingiverse.com/thing:5156081

## Encoder gear

Encoder gear

[60 teeth gear STEP file](https://github.com/kachurovskiy/nanoels/raw/main/h1/encoder/EncoderMount38.4mm-Wheel.step)

Check the distance between the spindle gear and the lathe housing: for the provided conical gear to fit, it has to be 23mm.

Encoder gear should fit loosely to the spindle allowing for it to move ~1 degree back and forth when the spindle is idle - it reduces the noise and forces applied to the encoder.

For spindles with 56 teeth, try [56 teeth gear model by kingjamez](https://www.thingiverse.com/thing:4754021).

# Stepper and driver

Cheap drivers like TB6600 are not recommended, they are very rough and noisy.

For H1 or H2 controllers it's suggested to buy the stepper that supports 200 steps mode. Microstepping will lower maximum usable rpm 2x for each microstep increase. I can recommend STEPPERONLINE steppers for good price and performance and their drivers usually support 200 step mode.

For H4 controller it's suggested to use [integrated closed loop motors like these](https://www.aliexpress.com/item/1005005598264428.html). They don't support 200 steps mode but H4 can easily run them at 800 steps per revolution. They don't need a separate driver, don't heat up and work quetly. They do take a but more space than open-loop steppers though.

## Stepper power supply

48V power supply is used on NEMA 23 for maximum power (check your driver max voltage) but 24V might also work for light turning. Closed loop motors require less current than open loop ones since they adjust to the load. For a lathe like WM210 with NEMA 23 and NEMA 17, 4A power supply would be sufficient.

## Stepper mount

Stepper mount

[STL file](https://github.com/kachurovskiy/nanoels/raw/main/h1/stepper/stepper-mount-nema23-28mm-hole.stl)

Dimensions of the lead screw front bearing housing for the provided 3D-printed part to fit: 28mm outside diameter, 12mm wide.

Stepper should rest on e.g. a piece of rubber when attached to the lathe - provided 3D printed part is only held by friction and is not designed to hold the full weight of the stepper long term.

A rock-solid but more expensive (35€) option is to order a 10mm steel laser cut out stepper mount: https://imgur.com/a/exO5Atl

It's also possible to cut out the stepper mount manually from plywood: https://imgur.com/a/CSmeSm2 ([PDF](https://github.com/kachurovskiy/nanoels/raw/main/h1/stepper/nema23-mount-plywood.pdf))

Alternative stepper mount with a pinch bolt: https://www.thingiverse.com/thing:5156087

## Cross-slide mount

See https://www.thingiverse.com/thing:6058899 - I use it with a 60mm open-loop NEMA 17 motor. It fits most desktop lathes like WM210.

It's good to insert a thin metal shim in the back to thermally sink the motor in to the lathe apron. Thickness of the shim can vary.

## Stepper to leadscrew

When connecting the gears, make sure to leave ~0.5mm space between them for optimal threading. This can be achieved e.g. by temporarily placing a piece of paper between them. Add grease and spread it between the gear teeth, remove the excess.

### Option 1: plastic gear

Stepper gear

[STL file](https://github.com/kachurovskiy/nanoels/raw/main/h1/stepper/stepper-gear-nema23-50t-10mm-10mm.stl)

This gear is designed to fit the NEMA 23 shaft (10mm diameter / 9.5mm narrow dimension) without any set screws. Gear is 10mm wide, entire part is 20mm wide.

Using this gear can be very noisy on certain RPMs.

### Option 2: adapter for the lathe gear

Stepper gear adapter

[STL file](https://github.com/kachurovskiy/nanoels/raw/main/h1/stepper/stepper-to-gear-adapter-12mm-10mm.stl)

If you have 2 metal gears that add up to 100 tooth together (e.g. 2x50 tooth gears) that came with the lathe, it's possible to simply use one of them on the leadscrew and one on the stepper with the help of the adapter above. It can be somewhat noisy on certain RPMs but otherwise works well.

### Option 3: HTD 5M belt connection

Stepper HTD 5M pulleys

[STL pulley 8mm bore](https://github.com/kachurovskiy/nanoels/raw/main/h1/stepper/htd5m-16t-8b.stl)

[STL pulley 10mm bore](https://github.com/kachurovskiy/nanoels/raw/main/h1/stepper/htd5m-16t-10b.stl)

[STL pulley 12mm bore](https://github.com/kachurovskiy/nanoels/raw/main/h1/stepper/htd5m-16t-12b.stl)

This is the best stepper to leadscrew connection method that I tried so far but it requires printing 2 parts above and buying a 180mm HTD 5M belt which is not expensive (2-10€) but can be hard to find.

This is the quietest option that also doesn't need greasing. 2 pulleys and a belt fit tight on the normal stepper mount shown above without a need for a tensioner.

16T-5M pulleys with various inner bore diameters are also available on AliExpress for 5-6€ each.

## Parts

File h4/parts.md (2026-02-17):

# Building H4 from individual parts

## Printed circuit boards

H4 consists of 2 PCBs - main one with ESP32 and keypad with push switches.

[Gerber, BOM, pick and place files](https://github.com/kachurovskiy/nanoels/tree/main/h4/pcbs) can be found in the `pcbs` folder. EasyEDA source files are also provided.

Edits I would make for the next batch:

- Make `R7` a `10Ohm` resistor for optimal buzzer volume and current usage
- Remove `F2`, `R12`, `R16`, `R36` and `R37` (or replace with 0 Ohm resistors) as they limit current on outgoing `5V` pins to the point where some encoders and motor drivers can't operate

Additionally, the following parts need to be ordered as they're not included in the PCB BOM:

- https://www.lcsc.com/product-detail/_XFCN-_C2915256.html (2x)
- https://www.lcsc.com/product-detail/_XFCN-_C2889983.html (2x)
- https://www.lcsc.com/product-detail/_DIBO-_C395832.html (5x)

## Front panel

I ordered the front panels on https://www.jrpanel.com/panel/buy/ with the following settings:



Provide them with [h4-go-1.png](https://github.com/kachurovskiy/nanoels/blob/main/h4/graphics/h4-go-1.png) as a design guidance and [h4-go-2.pdf](https://github.com/kachurovskiy/nanoels/blob/main/h4/graphics/h4-go-2.pdf) for printing purposes.

If you'd like to make modifications to the panel design, open [h4.fig](https://github.com/kachurovskiy/nanoels/blob/main/h4/graphics/h4.fig) using [figma.com](https://www.figma.com) editor.

## Rear sticker

I ordered the rear stickers on [Sticker Mule](https://www.stickermule.com/de/products/rechteck-sticker) using [h4-labels.pdf](https://github.com/kachurovskiy/nanoels/blob/main/h4/graphics/h4-labels.pdf) in 75x30mm size. It's doubled up due to their minimum size requirements. 

## Case

Plastic case consists of front and back piece which can be found in the [case folder](https://github.com/kachurovskiy/nanoels/tree/main/h4/case) as `STL` files ready for printing. If you'd like to modify the models, FreeCAD source file is also provided.

Front piece is designed to accept nine M3 threaded inserts, each 4mm long (4 to connect the back piece, 5 to hold the keypad). You would also need 9 M3 screws, each 8mm long.

Back piece accepts two M5 threaded inserts, each 5mm long with 8mm outside diameter.

h4 inserts

An optional small plastic shim model is also provided that is intended to be placed between the display and the keypad PCB to make the top row of buttons supported from the back.

Prints can also be ordered online e.g. on https://3d.jlcpcb.com/3d-printing-quote.

## Display

5V [HD44780 2004 LCD display](https://www.azdelivery.de/en/products/copy-of-hd44780-2004-lcd-display-bundle-4x20-zeichen) or similar is required. 16-pin 2.54mm header is used to connect it to the main PCB.

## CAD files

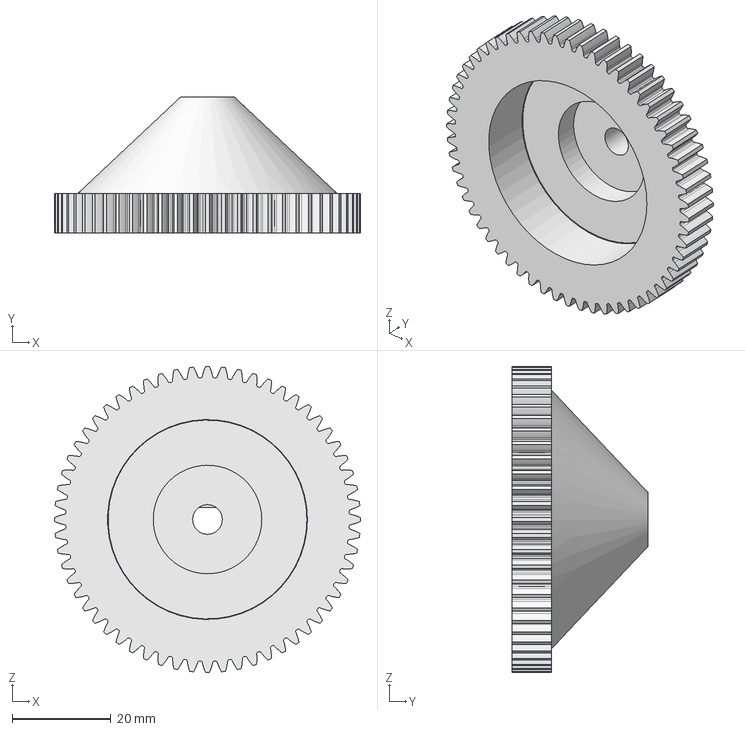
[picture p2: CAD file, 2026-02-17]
h1/encoder/EncoderMount38.4mm-Wheel.step
62.0 x 27.5 x 62.0 mm

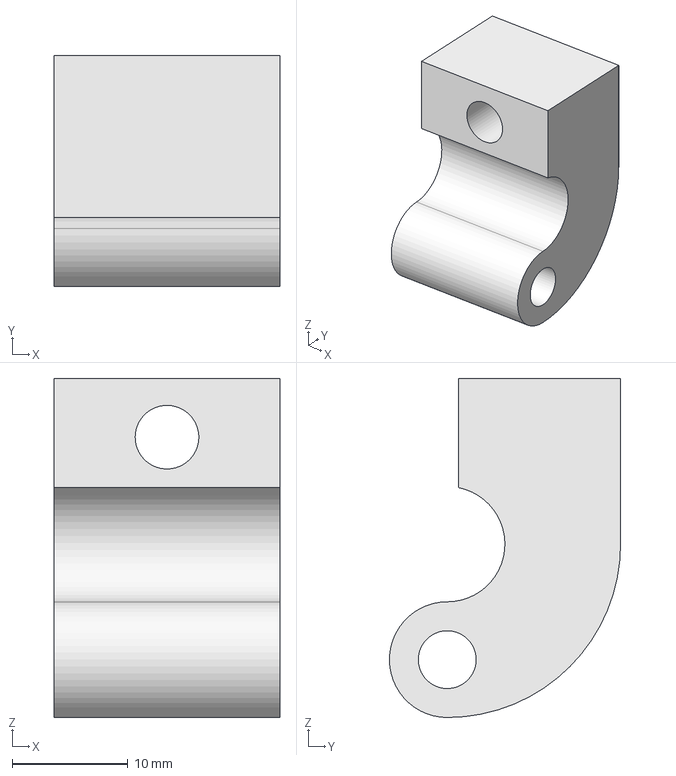
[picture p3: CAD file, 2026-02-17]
h5/case/h5mount2.step
19.5 x 20.0 x 29.3 mm

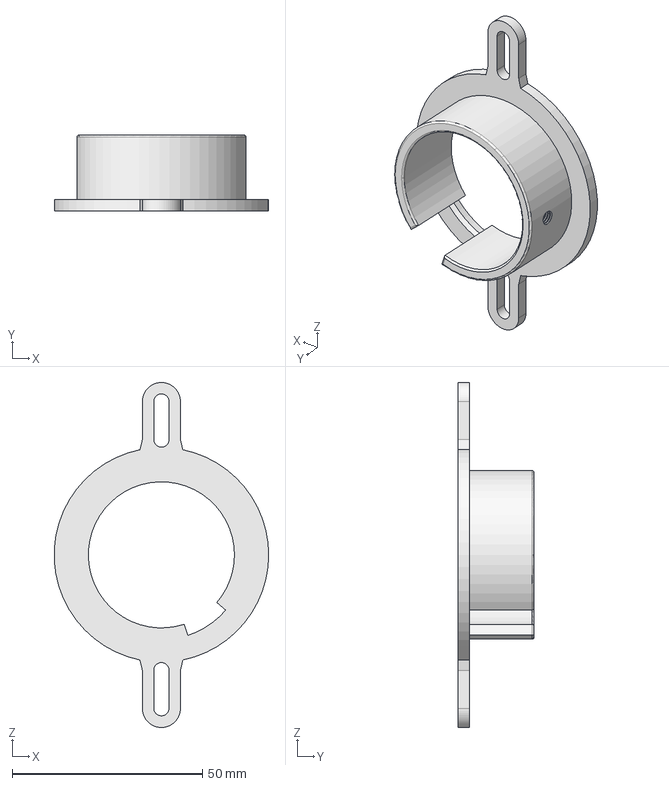
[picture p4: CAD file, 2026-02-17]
h1/encoder/EncoderMount38.4mm-Body.step
56.4 x 20.0 x 90.7 mm

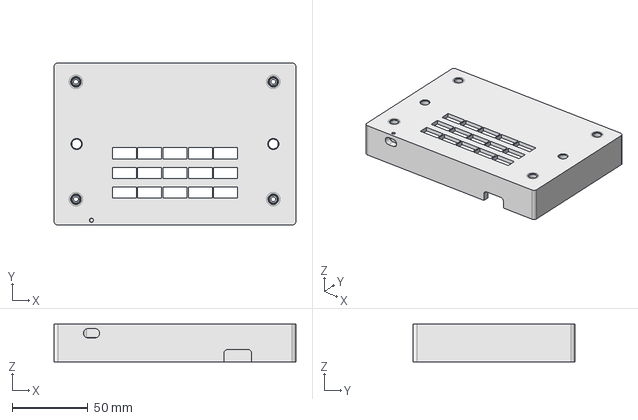
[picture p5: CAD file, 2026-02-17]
h5/case/h5case.step
160.0 x 107.0 x 25.0 mm

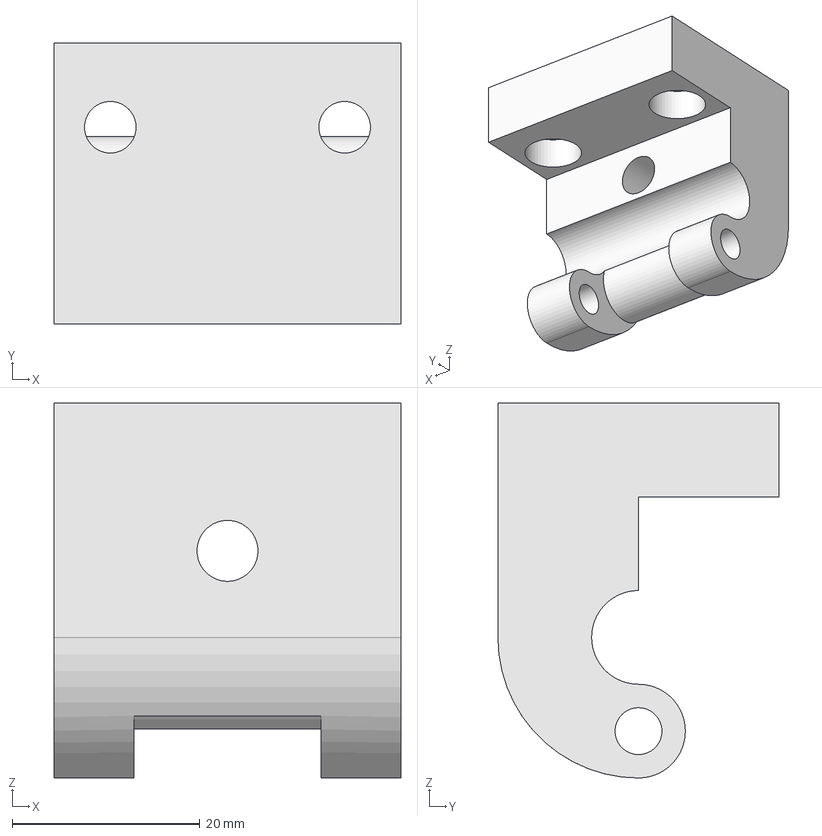
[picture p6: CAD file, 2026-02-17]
h5/case/h5mount1.step
37.0 x 30.0 x 40.0 mm

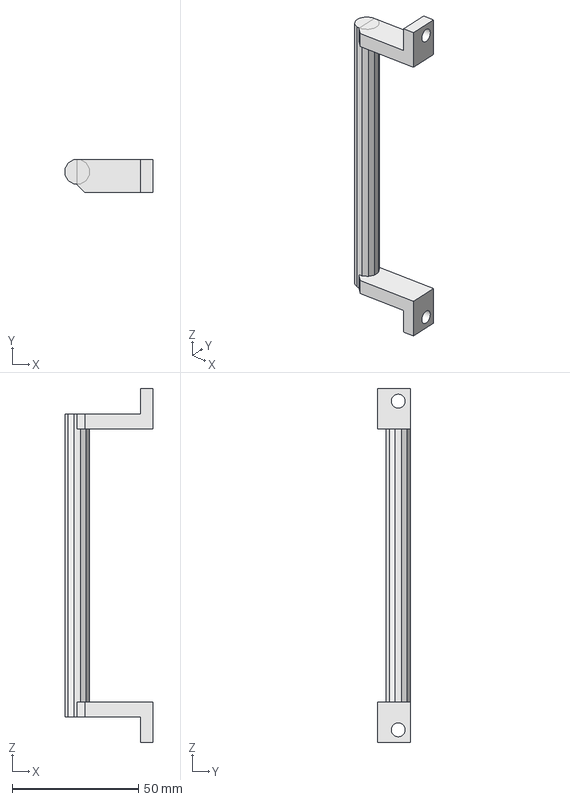
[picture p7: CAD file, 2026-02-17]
h5/case/h5handle.step
34.8 x 13.0 x 140.0 mm

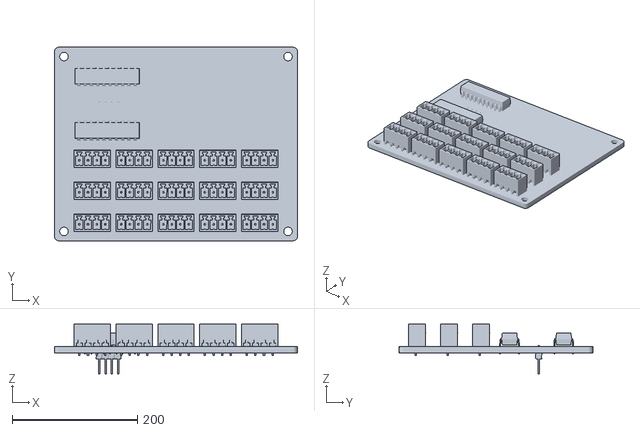
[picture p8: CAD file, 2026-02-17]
h5/case/pcb.obj
388.6 x 309.8 x 79.7

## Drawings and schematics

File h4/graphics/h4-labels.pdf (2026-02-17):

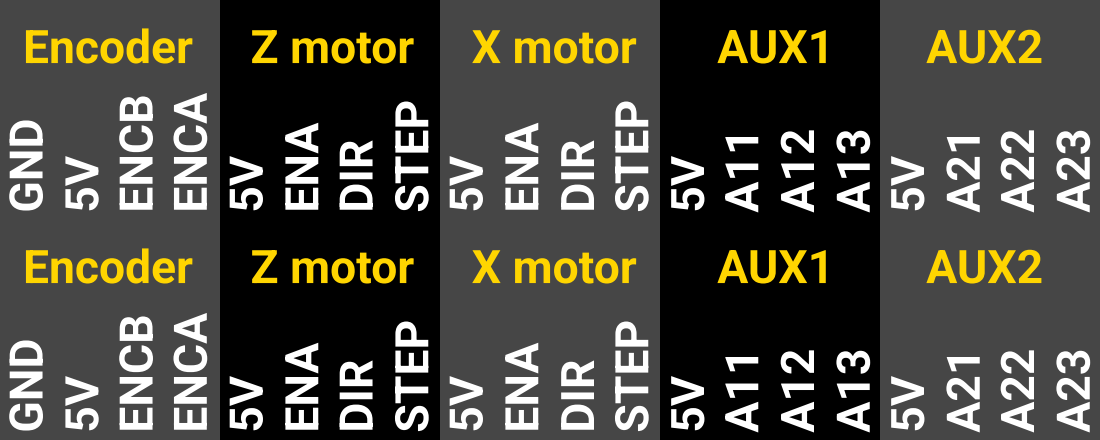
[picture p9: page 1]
GND; ENCB; ENCA; ENA; DIR; STEP; Encoder; Z motor; X motor; AUX1; AUX2

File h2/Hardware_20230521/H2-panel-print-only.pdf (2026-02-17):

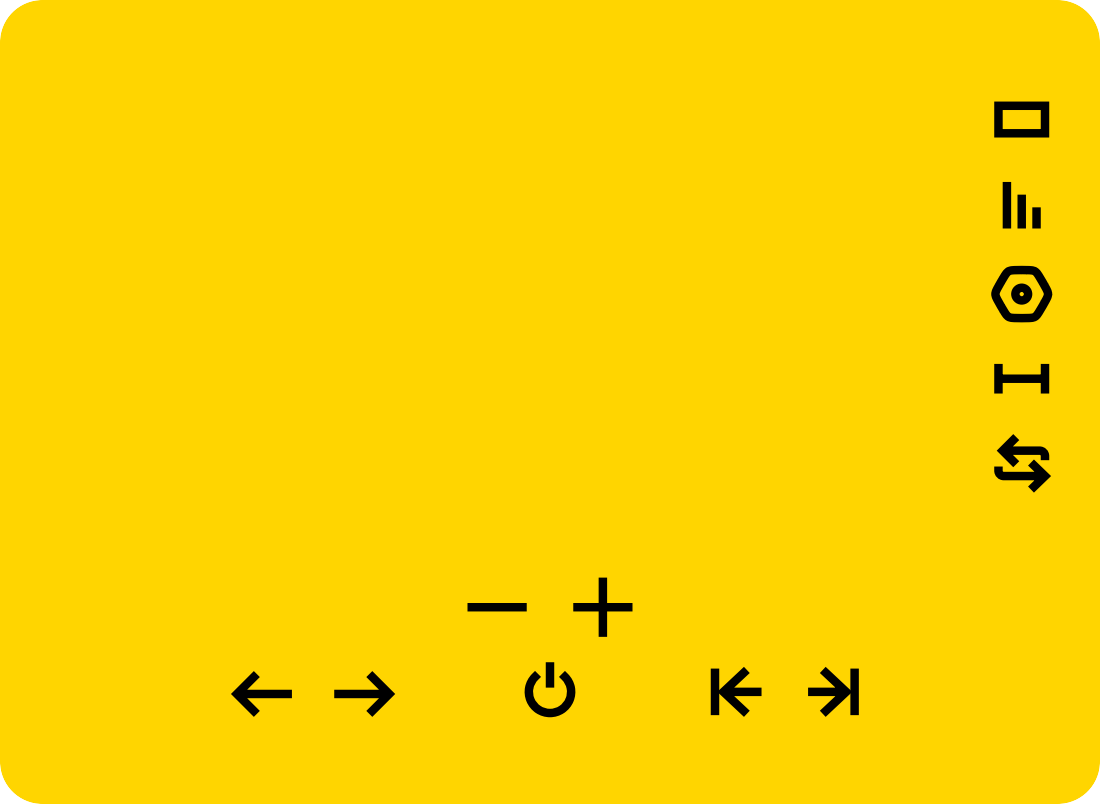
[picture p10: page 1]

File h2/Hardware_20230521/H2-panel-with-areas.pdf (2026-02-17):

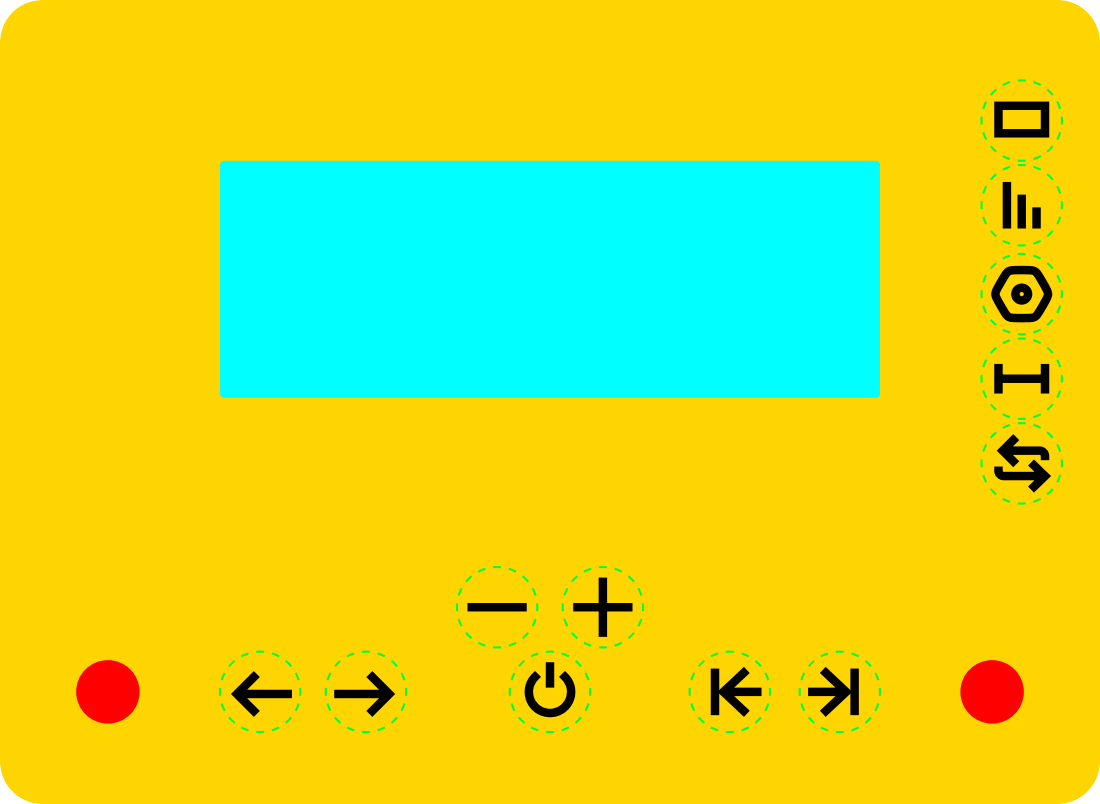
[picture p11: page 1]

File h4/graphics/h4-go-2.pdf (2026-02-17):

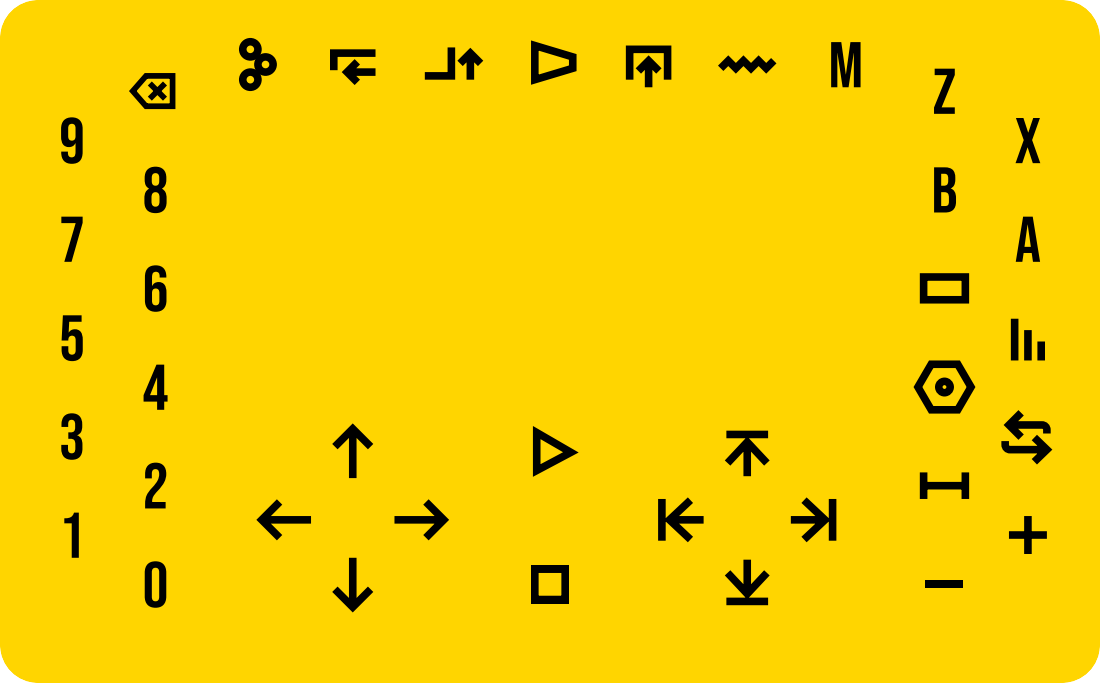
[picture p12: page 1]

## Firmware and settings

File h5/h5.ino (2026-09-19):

// https://github.com/kachurovskiy/nanoels

#include <config.h>

// Version of the pref storage format, should be changed when non-backward-compatible
// changes are made to the storage logic, resulting in Preferences wipe on first start.
#define PREFERENCES_VERSION 1
#define PREF_NAMESPACE "h5"

// GCode-related constants.
const float LINEAR_INTERPOLATION_PRECISION = 0.1; // 0 < x <= 1, smaller values make for quicker G0 and G1 moves
const long GCODE_WAIT_EPSILON_STEPS = 10;
const bool SPINDLE_PAUSES_GCODE = true; // pause GCode execution when spindle stops
const int GCODE_MIN_RPM = 30; // pause GCode execution if RPM is below this

// To be incremented whenever a measurable improvement is made.
#define SOFTWARE_VERSION 14

// To be changed whenever a different PCB / encoder / stepper / ... design is used.
#define HARDWARE_VERSION 5

// Spindle rotary encoder pins. Swap values if the rotation direction is wrong.
#define ENC_A 13
#define ENC_B 14

#define Z_ENA 41
#define Z_DIR 42
#define Z_STEP 35

#define Z_PULSE_A 18
#define Z_PULSE_B 8

#define JOYSTICK_I2C_ADDRESS 0x48
#define JOYSTICK_SDA 5
#define JOYSTICK_SCL 6
#define Z_JOYSTICK ADS1115_COMP_0_GND
#define X_JOYSTICK ADS1115_COMP_1_GND

#define X_ENA 16
#define X_DIR 15
#define X_STEP 7

#define X_PULSE_A 47
#define X_PULSE_B 21

#define Y_ENA 1
#define Y_DIR 2
#define Y_STEP 17

#define Y_PULSE_A 45
#define Y_PULSE_B 48

#define KEY_DATA 37
#define KEY_CLOCK 36

#define X_SCALE_A 40
#define X_SCALE_B 39

#define Z_SCALE_A 9
#define Z_SCALE_B 12

#define B_LEFT 21 // Left arrow - controls Z axis movement to the left
#define B_RIGHT 22 // Right arrow - controls Z axis movement to the right
#define B_UP 23 // Up arrow - controls X axis movement forwards
#define B_DOWN 24 // Down arrow - controls X axis movement backwards
#define B_FORWARD 85 // u - Advance Y axis
#define B_BACK 74 // j - Retreat Y axis
#define B_MINUS 60 // Numpad minus - recrements the pitch or number of passes
#define B_PLUS 95 // Numpad plus - increments the pitch or number of passes
#define B_ON 30 // Enter - starts operation or mode
#define B_OFF 27 // ESC - stops operation or mode
#define B_STOPL 65 // a - sets left stop
#define B_STOPR 68 // d - sets right stop
#define B_STOPU 87 // w - sets forward stop
#define B_STOPD 83 // s - sets rear stop
#define B_STOPF 73 // i - Y forward stop
#define B_STOPB 75 // k - Y backward stop
#define B_MULTISTART 84 // t - multi-start thread button
#define B_DISPL 12 // Win - changes info displayed in the bottom line (angle, rpm, ...)
#define B_STEP 64 // Tilda - changes distance moved when movement buttons are used
#define B_MEASURE 77 // m - controls metric / imperial / tpi
#define B_REVERSE 82 // r - changes pitch sign (left / right thread)
#define B_DIAMETER 79 // o - sets X0 so that centerline is at the middle of a given diameter value
#define B_0 48 // 0 top row - for number entry
#define B_1 49 // 1 top row
#define B_2 50 // ...
#define B_3 51
#define B_4 52
#define B_5 53
#define B_6 54
#define B_7 55
#define B_8 56
#define B_9 57
#define B_BACKSPACE 28 // removes the last entered number
#define B_MODE_GEARS 97 // F1 - sets the mode to gearbox
#define B_MODE_TURN 98 // F2 - ...
#define B_MODE_FACE 99 // F3
#define B_MODE_CONE 100 // F4
#define B_MODE_CUT 101 // F5
#define B_MODE_THREAD 102 // F6
#define B_MODE_ASYNC 103 // F7
#define B_MODE_ELLIPSE 104 // F8
#define B_MODE_GCODE 105 // F9
#define B_MODE_Y 106 // F10
#define B_MODE 107 // F11 - to cycle through modes
#define B_X 88 // x - zeroes X axis
#define B_Z 90 // z - zeroes Z axis
#define B_Y 72 // h - zeroes Y axis
#define B_X_ENA 67 // c - enables / disables X axis
#define B_Z_ENA 81 // q - enables / disables Z axis
#define B_Y_ENA 89 // y - enables / disables Y axis

#define PREF_VERSION "v"
#define PREF_DUPR "d"
#define PREF_POS_Z "zp"
#define PREF_LEFT_STOP_Z "zls"
#define PREF_RIGHT_STOP_Z "zrs"
#define PREF_ORIGIN_POS_Z "zpo"
#define PREF_POS_GLOBAL_Z "zpg"
#define PREF_MOTOR_POS_Z "zpm"
#define PREF_DISABLED_Z "zd"
#define PREF_POS_X "xp"
#define PREF_LEFT_STOP_X "xls"
#define PREF_RIGHT_STOP_X "xrs"
#define PREF_ORIGIN_POS_X "xpo"
#define PREF_POS_GLOBAL_X "xpg"
#define PREF_MOTOR_POS_X "xpm"
#define PREF_DISABLED_X "xd"
#define PREF_POS_Y "y1p"
#define PREF_LEFT_STOP_Y "y1ls"
#define PREF_RIGHT_STOP_Y "y1rs"
#define PREF_ORIGIN_POS_Y "y1po"
#define PREF_POS_GLOBAL_Y "y1pg"
#define PREF_MOTOR_POS_Y "y1pm"
#define PREF_DISABLED_Y "y1d"
#define PREF_SPINDLE_POS "sp"
#define PREF_SPINDLE_POS_AVG "spa"
#define PREF_OUT_OF_SYNC "oos"
#define PREF_SPINDLE_POS_GLOBAL "spg"
#define PREF_SHOW_ANGLE "ang"
#define PREF_SHOW_TACHO "rpm"
#define PREF_STARTS "sta"
#define PREF_MODE "mod"
#define PREF_MEASURE "mea"
#define PREF_CONE_RATIO "cr"
#define PREF_TURN_PASSES "tp"
#define PREF_MOVE_STEP "ms"
#define PREF_AUX_FORWARD "af"
#define PREF_X_SCALE_COUNT "xsc"
#define PREF_Z_SCALE_COUNT "zsc"

#define MOVE_STEP_1 10000 // 1mm
#define MOVE_STEP_2 1000 // 0.1mm
#define MOVE_STEP_3 100 // 0.01mm

#define MOVE_STEP_IMP_1 25400 // 1/10"
#define MOVE_STEP_IMP_2 2540 // 1/100"
#define MOVE_STEP_IMP_3 254 // 1/1000" also known as 1 thou

#define MODE_NORMAL 0
#define MODE_ASYNC 2
#define MODE_CONE 3
#define MODE_TURN 4
#define MODE_FACE 5
#define MODE_CUT 6
#define MODE_THREAD 7
#define MODE_ELLIPSE 8
#define MODE_GCODE 9
#define MODE_Y 10

#define MEASURE_METRIC 0
#define MEASURE_INCH 1
#define MEASURE_TPI 2

#define ESTOP_NONE 0
#define ESTOP_POS 2
#define ESTOP_MARK_ORIGIN 3
#define ESTOP_ON_OFF 4
#define ESTOP_OFF_MANUAL_MOVE 5

#define TIMER_FREQ 1000000 // 1MHz async timer frequency

struct CircleBuffer {
  char* buffer;
  size_t head;
  size_t tail;
  size_t size;
};

#include <FS.h>
#include <LittleFS.h>
#include <WiFi.h>
#include <WebServer.h>
#include <WebSocketsServer.h> // install via Libraries as "WebSockets"
#include <driver/pcnt.h>
#include <Preferences.h>
#include <PS2KeyAdvanced.h> // install via Libraries as "PS2KeyAdvanced"

#include <esp_wifi.h>
#include <SPIFFS.h>
#include <Update.h>

#include<ADS1115_WE.h> 
#include<Wire.h>

#include "esp_system.h"
#include "soc/rtc_cntl_reg.h"

ADS1115_WE adc = ADS1115_WE(JOYSTICK_I2C_ADDRESS);

#include "indexhtml.h"

#define FORMAT_LITTLEFS_IF_FAILED true

// For MEASURE_TPI, round TPI to the nearest integer if it's within this range of it.
// E.g. 80.02tpi would be shown as 80tpi but 80.04tpi would be shown as-is.
const float TPI_ROUND_EPSILON = 0.03;

const float ENCODER_STEPS_FLOAT = ENCODER_STEPS_INT; // Convenience float version of ENCODER_STEPS_INT
const long RPM_BULK = ENCODER_STEPS_INT; // Measure RPM averaged over this number of encoder pulses

const long GCODE_FEED_DEFAULT_DU_SEC = 20000; // Default feed in du/sec in GCode mode
const float GCODE_FEED_MIN_DU_SEC = 167; // Minimum feed in du/sec in GCode mode - F1

#define DHIGH(x) digitalWrite(x, HIGH)
#define DLOW(x) digitalWrite(x, LOW)

#define DELAY(x) vTaskDelay(x / portTICK_PERIOD_MS);

#define LCD_HASH_INITIAL -3845709 // Random number that's unlikely to naturally occur as an actual hash
long lcdHashLine0 = LCD_HASH_INITIAL;
long lcdHashLine1 = LCD_HASH_INITIAL;
long lcdHashLine2 = LCD_HASH_INITIAL;
long lcdHashLine3 = LCD_HASH_INITIAL;
long lcdHashLineAxis = LCD_HASH_INITIAL;
bool splashScreen = false;

unsigned long keypadTimeUs = 0;

// Most buttons we only have "down" handling, holding them has no effect.
// Buttons with special "holding" logic have flags below.
bool buttonLeftPressed = false;
bool buttonRightPressed = false;
bool buttonUpPressed = false;
bool buttonDownPressed = false;
bool buttonOffPressed = false;
bool buttonBackPressed = false;
bool buttonForwardPressed = false;

bool inNumpad = false;
int numpadDigits[20];
int numpadIndex = 0;

bool isOn = false;
bool nextIsOn; // isOn value that should be applied asap
bool nextIsOnFlag; // whether nextIsOn requires attention
unsigned long resetMillis = 0;
int emergencyStop = 0;

bool beepFlag = false; // allows time-critical code to ask for a beep on another core

long dupr = 0; // pitch, tenth of a micron per rotation
long savedDupr = 0; // dupr saved in Preferences
long nextDupr = dupr; // dupr value that should be applied asap
bool nextDuprFlag = false; // whether nextDupr requires attention

SemaphoreHandle_t motionMutex; // controls blocks of code where variables affecting the motion loop() are changed

int starts = 1; // number of starts in a multi-start thread
int savedStarts = 0; // starts saved in Preferences
int nextStarts = starts; // number of starts that should be used asap
bool nextStartsFlag = false; // whether nextStarts requires attention

TaskHandle_t taskDisplayHandle = NULL;
void setText(const String &id, const String &text);
void toScreen(const String &command);
char uploadProgress[7] = "/-\|/-\|";
int progressIndex = 0;
int tftBufCurrentSize = 0;
uint8_t tftBuf[4096];

struct Axis {
  SemaphoreHandle_t mutex;

  char name;
  bool active;
  bool rotational;
  float motorSteps; // motor steps per revolution of the axis
  float screwPitch; // lead screw pitch in deci-microns (10^-7 of a meter)

  long pos; // relative position of the tool in stepper motor steps
  long savedPos; // value saved in Preferences
  float fractionalPos; // fractional distance in steps that we meant to travel but couldn't
  long originPos; // relative position of the stepper motor to origin, in steps
  long savedOriginPos; // originPos saved in Preferences
  long posGlobal; // global position of the motor in steps
  long savedPosGlobal; // posGlobal saved in Preferences
  int pendingPos; // steps of the stepper motor that we should make as soon as possible
  long motorPos; // position of the motor in stepper motor steps, same as pos unless moving back, then differs by backlashSteps
  long savedMotorPos; // motorPos saved in Preferences
  bool continuous; // whether current movement is expected to continue until an unknown position

  long leftStop; // left stop value of pos
  long savedLeftStop; // value saved in Preferences
  long nextLeftStop; // left stop value that should be applied asap
  bool nextLeftStopFlag; // whether nextLeftStop required attention

  long rightStop; // right stop value of pos
  long savedRightStop; // value saved in Preferences
  long nextRightStop; // right stop value that should be applied asap
  bool nextRightStopFlag; // whether nextRightStop requires attention

  long speed; // motor speed in steps / second
  long speedStart; // Initial speed of a motor, steps / second.
  long speedMax; // To limit max speed e.g. for manual moves
  long speedManualMove; // Maximum speed of a motor during manual move, steps / second.
  long acceleration; // Acceleration of a motor, steps / second ^ 2.
  long decelerateSteps; // Number of steps before the end position the deceleration should start.

  bool direction; // To reset speed when direction changes.
  bool directionInitialized;
  unsigned long stepStartUs;
  int stepperEnableCounter;
  bool disabled;
  bool savedDisabled;

  bool invertStepper; // change (true/false) if the carriage moves e.g. "left" when you press "right".
  bool invertEnable; // change (true/false) if the Enable pin is inverted
  bool needsRest; // set to false for closed-loop drivers, true for open-loop.
  bool movingManually; // whether stepper is being moved by left/right buttons
  long estopSteps; // amount of steps to exceed machine limits
  long backlashSteps; // amount of steps in reverse direction to re-engage the carriage
  long gcodeRelativePos; // absolute position in steps that relative GCode refers to

  int ena; // Enable pin of this motor
  int dir; // Direction pin of this motor
  int step; // Step pin of this motor

  int pulseA;
  int pulseB;
  int pulseCount;
  pcnt_unit_t pulseUnit;
};

void initAxis(Axis* a, char name, bool active, bool rotational, float motorSteps, float screwPitch, long speedStart, long speedManualMove,
    long acceleration, bool invertStepper, bool invertEnable, bool needsRest, long maxTravelMm, long backlashDu, int ena, int dir, int step, int pulseA, int pulseB, pcnt_unit_t pulseUnit) {
  a->mutex = xSemaphoreCreateMutex();

  a->name = name;
  a->active = active;
  a->rotational = rotational;
  a->motorSteps = motorSteps;
  a->screwPitch = screwPitch;

  a->pos = 0;
  a->savedPos = 0;
  a->fractionalPos = 0.0;
  a->originPos = 0;
  a->savedOriginPos = 0;
  a->posGlobal = 0;
  a->savedPosGlobal = 0;
  a->pendingPos = 0;
  a->motorPos = 0;
  a->savedMotorPos = 0;
  a->continuous = false;

  a->leftStop = 0;
  a->savedLeftStop = 0;
  a->nextLeftStopFlag = false;

  a->rightStop = 0;
  a->savedRightStop = 0;
  a->nextRightStopFlag = false;

  a->speed = speedStart;
  a->speedStart = speedStart;
  a->speedMax = LONG_MAX;
  a->speedManualMove = speedManualMove;
  a->acceleration = acceleration;
  a->decelerateSteps = 0;
  long s = speedManualMove;
  while (s > speedStart) {
    a->decelerateSteps++;
    s -= a->acceleration / float(s);
  }

  a->direction = true;
  a->directionInitialized = false;
  a->stepStartUs = 0;
  a->stepperEnableCounter = 0;
  a->disabled = false;
  a->savedDisabled = false;

  a->invertStepper = invertStepper;
  a->invertEnable = invertEnable;
  a->needsRest = needsRest;
  a->movingManually = false;
  a->estopSteps = maxTravelMm * 10000 / a->screwPitch * a->motorSteps;
  a->backlashSteps = backlashDu * a->motorSteps / a->screwPitch;
  a->gcodeRelativePos = 0;

  a->ena = ena;
  a->dir = dir;
  a->step = step;

  a->pulseA = pulseA;
  a->pulseB = pulseB;
  a->pulseUnit = pulseUnit;
  a->pulseCount = 0;
}

Axis z;
Axis x;
Axis y;

unsigned long saveTime = 0; // micros() of the previous Prefs write
unsigned long spindleEncTime = 0; // micros() of the previous spindle update
unsigned long spindleEncTimeDiffBulk = 0; // micros() between RPM_BULK spindle updates
unsigned long spindleEncTimeAtIndex0 = 0; // micros() when spindleEncTimeIndex was 0
int spindleEncTimeIndex = 0; // counter going between 0 and RPM_BULK - 1
long spindlePos = 0; // Spindle position
long spindlePosAvg = 0; // Spindle position accounting for encoder backlash
long savedSpindlePosAvg = 0; // spindlePosAvg saved in Preferences
long savedSpindlePos = 0; // spindlePos value saved in Preferences
int spindleCount = 0; // Last processed spindle encoder pulse counter value.
int spindlePosSync = 0; // Non-zero if gearbox is on and a soft limit was removed while axis was on it
int savedSpindlePosSync = 0; // spindlePosSync saved in Preferences
long spindlePosGlobal = 0; // global spindle position that is unaffected by e.g. zeroing
long savedSpindlePosGlobal = 0; // spindlePosGlobal saved in Preferences

bool showAngle = false; // Whether to show 0-359 spindle angle on screen
bool showTacho = false; // Whether to show spindle RPM on screen
bool savedShowAngle = false; // showAngle value saved in Preferences
bool savedShowTacho = false; // showTacho value saved in Preferences
int shownRpm = 0;
unsigned long shownRpmTime = 0; // micros() when shownRpm was set

long moveStep = 0; // in deci-microns
long savedMoveStep = 0; // moveStep saved in Preferences

volatile int mode = -1; // mode of operation (ELS, multi-start ELS, asynchronous)
int nextMode = 0; // mode value that should be applied asap
bool nextModeFlag = false; // whether nextMode needs attention
int savedMode = -1; // mode saved in Preferences

int measure = MEASURE_METRIC; // Whether to show distances in inches
int savedMeasure = MEASURE_METRIC; // measure value saved in Preferences

float coneRatio = 1; // In cone mode, how much X moves for 1 step of Z
float savedConeRatio = 0; // value of coneRatio saved in Preferences
float nextConeRatio = 0; // coneRatio that should be applied asap
bool nextConeRatioFlag = false; // whether nextConeRatio requires attention

int turnPasses = 3; // In turn mode, how many turn passes to make
int savedTurnPasses = 0; // value of turnPasses saved in Preferences

long setupIndex = 0; // Index of automation setup step
bool auxForward = true; // True for external, false for internal thread
bool savedAuxForward = false; // value of auxForward saved in Preferences

long opIndex = 0; // Index of an automation operation
bool opIndexAdvanceFlag = false; // Whether user requested to move to the next pass
long opSubIndex = 0; // Sub-index of an automation operation
int opDuprSign = 1; // 1 if dupr was positive when operation started, -1 if negative
long opDupr = 0; // dupr that the multi-pass operation started with

String gcodeCommand = "";
long gcodeFeedDuPerSec = GCODE_FEED_DEFAULT_DU_SEC;
bool gcodeInitialized = false;
bool gcodeAbsolutePositioning = true;
bool gcodeInBrace = false;
bool gcodeInSemicolon = false;
bool wsInKeycode = false;
int wsKeycode = 0;
String keycodeCommand = "";
bool gcodeInSave = false;
bool gcodeInSaveFirstLine = false;
String gcodeSaveName = "";
String gcodeSaveValue = "";
int gcodeProgramIndex = 0;
int gcodeProgramCount = 0;
String gcodeProgram = "";
int gcodeProgramCharIndex = 0;

PS2KeyAdvanced keyboard;

hw_timer_t *async_timer = timerBegin(TIMER_FREQ);
bool timerAttached = false;

CircleBuffer inBuffer;
CircleBuffer outBuffer;

int xScaleCount = 0;
int savedXScaleCount = 0;

int zScaleCount = 0;
int savedZScaleCount = 0;


bool bufferAvailable(CircleBuffer* b) {
  return b->head != b->tail;
}

bool writeBuffer(CircleBuffer* b, char c) {
  if ((b->head + 1) % b->size == b->tail) {
    return false;
  }
  b->buffer[b->head] = c;
  b->head = (b->head + 1) % b->size;
  return true;
}

bool writeBuffer(CircleBuffer* b, const char* str) {
  while (*str) {
    if (!writeBuffer(b, *str++)) {
      return false;
    }
  }
  return true;
}

bool writeBuffer(CircleBuffer* b, const String& str) {
  return writeBuffer(b, str.c_str());
}

bool writeBuffer(CircleBuffer* b, float f, int precision) {
  char buffer[16];
  dtostrf(f, 0, precision, buffer);
  return writeBuffer(b, buffer);
}

char shiftBuffer(CircleBuffer* b) {
  if (b->head == b->tail) {
    return 0;
  }
  char c = b->buffer[b->tail];
  b->tail = (b->tail + 1) % b->size;
  return c;
}

void initBuffer(CircleBuffer* b, size_t size) {
  b->size = size;
  b->buffer = (char*)malloc(size);
  b->head = 0;
  b->tail = 0;
}

void clearBuffer(CircleBuffer* b) {
  b->head = 0;
  b->tail = 0;
}

WebServer server(80);
WebSocketsServer webSocket(81);
String wifiStatus = "No WiFi";
unsigned long wifiStatusMillis = 0;

void handleWebSocketEvent(uint8_t num, WStype_t type, uint8_t* payload, size_t length) {
  if (type == WStype_TEXT) {
    for (size_t i = 0; i < length; i++) {
      writeBuffer(&inBuffer, payload[i]);
    }
  }
}

void handleClientRequests() {
  server.send(200, "text/html", indexhtml);
}

int getGcodeProgramCount() {
  File root = LittleFS.open("/");
  if (!root || !root.isDirectory()) {
    writeBuffer(&outBuffer, "error: failed to open directory\n");
    return 0;
  }

  int count = 0;
  File file = root.openNextFile();
  while (file) {
    String filename = file.name();
    file.close();
    if (filename.endsWith(".gcode")) {
      count++;
    }
    file = root.openNextFile();
  }

  return count;
}

bool saveGcode() {
  if (gcodeSaveName.length() < 2) {
    writeBuffer(&outBuffer, "error: name must be at least 2 chars\n");
    return false;
  }
  if (gcodeSaveValue.length() < 2) {
    writeBuffer(&outBuffer, "error: program too short\n");
    return false;
  }

  String filename = "/" + gcodeSaveName + ".gcode";
  File file = LittleFS.open(filename, "w");
  if (!file) {
    writeBuffer(&outBuffer, "error: failed to open file\n");
    return false;
  }

  file.print(gcodeSaveValue);
  file.close();

  writeBuffer(&outBuffer, "success: G-code saved\n");
  gcodeProgramCount = getGcodeProgramCount();
  return true;
}

bool removeGcodeByName(const String& name) {
  if (name.length() == 0) return false;

  String filename = "/" + name + ".gcode";
  if (!LittleFS.exists(filename)) {
    writeBuffer(&outBuffer, "error: file not found\n");
    return false;
  }

  if (!LittleFS.remove(filename)) {
    writeBuffer(&outBuffer, "error: failed to delete " + filename + "\n");
    return false;
  }

  writeBuffer(&outBuffer, "success: " + name + " deleted\n");
  gcodeProgramCount = getGcodeProgramCount();
  return true;
}

String readGcodeProgram(const String& name) {
  String filename = "/" + name + ".gcode";
  File file = LittleFS.open(filename, "r");
  if (!file) {
    return "";
  }

  String result;
  result.reserve(file.size());
  char buf[64];
  while (file.available()) {
    size_t bytesRead = file.readBytes(buf, sizeof(buf));
    result += String(buf).substring(0, bytesRead);
  }
  file.close();
  return result;
}

void handleGcodeAdd() {
  if (server.hasArg("name") && server.hasArg("gcode")) {
    gcodeSaveName = server.arg("name");
    gcodeSaveValue = server.arg("gcode");
    if (saveGcode()) {
      server.send(200, "text/plain", "G-code saved successfully");
    } else {
      server.send(500, "text/plain", "Failed to save G-code");
    }
  } else {
    server.send(400, "text/plain", "Missing parameters");
  }
}
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
void loop() {
  if (emergencyStop != ESTOP_NONE) {
    return;
  }
  if (xSemaphoreTake(motionMutex, 1) != pdTRUE) {
    return;
  }
  applySettings();
  processSpindleCounter();
  processXScaleCounter();
  processZScaleCounter();
  discountFullSpindleTurns();
  if (!isOn || dupr == 0 || spindlePosSync != 0) {
    // None of the modes work.
  } else if (mode == MODE_NORMAL) {
    modeGearbox();
  } else if (mode == MODE_TURN) {
    modeTurn(&z, &x);
  } else if (mode == MODE_FACE) {
    modeTurn(&x, &z);
  } else if (mode == MODE_CUT) {
    modeCut();
  } else if (mode == MODE_CONE) {
    modeCone();
  } else if (mode == MODE_THREAD) {
    modeTurn(&z, &x);
  } else if (mode == MODE_ELLIPSE) {
    modeEllipse(&z, &x);
  }
  moveAxis(&z);
  moveAxis(&x);
  if (ACTIVE_Y) moveAxis(&y);
  xSemaphoreGive(motionMutex);
}

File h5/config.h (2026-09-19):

/* Change values in this section to suit your hardware. */

#include <driver/pcnt.h>

//#define NEXTION_BAUDRATE 115200
//#define NEXTION_BAUDRATE 250000
#define NEXTION_BAUDRATE 921600

#define ENCODER_SINGLE 1
#define ENCODER_HALF 2
#define ENCODER_FULL 4

// Define your hardware parameters here.
const int ENCODER_PPR = 600; // 1200 step spindle optical rotary encoder. Fractional values not supported.
const int ENCODER_BACKLASH = 0; // Numer of impulses encoder can issue without movement of the spindle
const int ENCODER_TYPE = ENCODER_SINGLE; // 1 - Single (A channel falling edge count only),
                            // 2 - halfQuad (A channel falling and rising edges count)
                            // 4 - fullQuad (falling and rising edges count on both channels)
const int ENCODER_SPINDLE_RATIO = 4;

const long MOTOR_SCREW_RATIO_Z = 3;

// Main lead screw (Z) parameters.
const long SCREW_Z_DU = 20000 / MOTOR_SCREW_RATIO_Z; // 2mm --4mm SFU1204 ball screw in deci-microns (10^-7 of a meter)
const long MOTOR_STEPS_Z = 800;
const long SPEED_START_Z = MOTOR_STEPS_Z; // Initial speed of a motor, steps / second.
const long ACCELERATION_Z = 20 * MOTOR_STEPS_Z; // Acceleration of a motor, steps / second ^ 2.
const long SPEED_MANUAL_MOVE_Z = 6 * MOTOR_STEPS_Z; // Maximum speed of a motor during manual move, steps / second.
const bool INVERT_Z = false; // change (true/false) if the carriage moves e.g. "left" when you press "right".
const bool INVERT_Z_ENABLE = false; // change (true/false) if the Z axis enable pin is inverted
const bool NEEDS_REST_Z = false; // Set to false for closed-loop drivers, true for open-loop.
const long MAX_TRAVEL_MM_Z = 300; // Lathe bed doesn't allow to travel more than this in one go, 30cm / ~1 foot
const long BACKLASH_DU_Z = 15700; //14500; // 0mm backlash in deci-microns (10^-7 of a meter)
const char NAME_Z = 'Z'; // Text shown on screen before axis position value, GCode axis name

// Cross-slide lead screw (X) parameters.
const long SCREW_X_DU = 10000; // 4mm SFU1204 ball screw in deci-microns (10^-7 of a meter)
const long MOTOR_STEPS_X = 800;
const long SPEED_START_X = MOTOR_STEPS_X; // Initial speed of a motor, steps / second.
const long ACCELERATION_X = 20 * MOTOR_STEPS_X; // Acceleration of a motor, steps / second ^ 2.
const long SPEED_MANUAL_MOVE_X = 6 * MOTOR_STEPS_X; // Maximum speed of a motor during manual move, steps / second.
const bool INVERT_X = true; // change (true/false) if the carriage moves e.g. "left" when you press "right".
const bool INVERT_X_ENABLE = false; // change (true/false) if the X axis enable pin is inverted
const bool NEEDS_REST_X = false; // Set to false for all kinds of drivers or X will be unlocked when not moving.
const long MAX_TRAVEL_MM_X = 100; // Cross slide doesn't allow to travel more than this in one go, 10cm
const long BACKLASH_DU_X = 0; // 0.15mm backlash in deci-microns (10^-7 of a meter)
const char NAME_X = 'X'; // Text shown on screen before axis position value, GCode axis name

// Manual stepping with left/right/up/down buttons. Only used when step isn't default continuous (1mm or 0.1").
const long STEP_TIME_MS = 500; // Time in milliseconds it should take to make 1 manual step.
const long DELAY_BETWEEN_STEPS_MS = 120; // Time in milliseconds to wait between steps.

// Connect to WiFi and expose web UI to control and receive GCode.
const bool WIFI_ENABLED = true;
const char* SSID = "Wanda2G";
const char* PASSWORD = "jetpet22";
const long INCOMING_BUFFER_SIZE = 100000;
const long OUTGOING_BUFFER_SIZE = 100000;
const char* WIFI_HOSTNAME = "nanoELS";
const char* WIFI_COUNTRY = "CA";
const long WIFI_SCHANNEL = 1;
const long WIFI_NCHANNEL = 165;

/* Changing anything below shouldn't be needed for basic use. */
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

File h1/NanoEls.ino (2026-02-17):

// https://github.com/kachurovskiy/nanoels

/* Change values in this section to suit your hardware. */

// Define your hardware parameters here. Don't remove the ".0" at the end.
#define ENCODER_STEPS 600.0 // 600 step spindle optical rotary encoder
#define MOTOR_STEPS 200.0 // 200 step stepper motor, no microstepping
#define LEAD_SCREW_HMM 200.0 // 2mm lead screw

// Tweak these values to move display picture around to center it in the window.
// Acceptable values 0 to ~10 pixels, anything higher and text will be cropped.
#define DISPLAY_LEFT 4
#define DISPLAY_TOP 4

// Spindle rotary encoder pins. Nano only supports interrupts on D2 and D3.
// Swap values if the rotation direction is wrong.
#define ENC_A 3 // D3
#define ENC_B 2 // D2

// Stepper pulse and acceleration constants.
#define PULSE_MIN_US round(500 * (200.0 / MOTOR_STEPS)) // Microseconds to wait after high pulse, min.
#define PULSE_MAX_US round(2000 * (200.0 / MOTOR_STEPS)) // Microseconds to wait after high pulse, max. Slow start.
#define PULSE_DELTA_US 7 // Microseconds remove from waiting time on every step. Acceleration.
#define INVERT_STEPPER true // false for 1:1 geared connection, true for 1:1 belt connection

// Pitch shortcut buttons, set to your most used values that should be available within 1 click.
#define F3_PITCH 10 // 0.1mm
#define F4_PITCH 100 // 1mm
#define F5_PITCH 200 // 2mm

// Uncomment if you're using a big LCD2004 display.
// #define LCD

/* Changing anything below shouldn't be needed for basic use. */

#define LONG_MIN long(-2147483648)
#define LONG_MAX long(2147483647)

#define LOOP_COUNTER_MAX 1500 // 1500 loops without stepper move to start reading buttons
#define HMMPR_MAX 1000 // 10mm

// Ratios between spindle and stepper.
#define ENCODER_TO_STEPPER_STEP_RATIO MOTOR_STEPS / (LEAD_SCREW_HMM * ENCODER_STEPS)
#define STEPPER_TO_ENCODER_STEP_RATIO LEAD_SCREW_HMM * ENCODER_STEPS / MOTOR_STEPS

// If time between encoder ticks is less than this, direction change is not allowed.
// Effectively this limits direction change to the time when spindle is <20rpm.
#define DIR_CHANGE_DIFF_MS (int) (5 * ENCODER_STEPS / 600)

// Version of the EEPROM storage format, should be changed when non-backward-compatible
// changes are made to the storage logic, resulting in EEPROM wipe on first start.
#define EEPROM_VERSION 2

// To be incremented whenever a measurable improvement is made.
#define SOFTWARE_VERSION 9

// To be changed whenever a different PCB / encoder / stepper / ... design is used.
#define HARDWARE_VERSION 1

#define DIR A0
#define STEP A1

#define LEFT 11
#define ONOFF 10
#define RIGHT A3

#define LEFT_STOP 7
#define RIGHT_STOP 9

#define F1 6
#define F2 5
#define F3 4
#define F4 12
#define F5 8

#define ADDR_EEPROM_VERSION 0 // takes 1 byte
#define ADDR_ONOFF 1 // takes 1 byte
#define ADDR_HMMPR 2 // takes 2 bytes
#define ADDR_POS 4 // takes 4 bytes
#define ADDR_LEFT_STOP 8 // takes 4 bytes
#define ADDR_RIGHT_STOP 12 // takes 4 bytes
#define ADDR_SPINDLE_POS 16 // takes 4 bytes
#define ADDR_OUT_OF_SYNC 20 // takes 2 bytes
#define ADDR_SHOW_ANGLE 22 // takes 1 byte

// Uncomment to print out debug info in Serial.
// #define DEBUG

// Uncomment to run the self-test of the code instead of the actual program.
// #define TEST
#ifdef TEST
  bool mockDigitalPins[20] = {0};
  int mockDigitalPinToggleOnRead = -1;
  int mockDigitalRead(int x) {
    int value = mockDigitalPins[x];
    if (x == mockDigitalPinToggleOnRead) {
      mockDigitalPins[x] ^= 1;
    }
    return value;
  }
  #define DREAD(x) mockDigitalRead(x)
#else
  #include <FastGPIO.h>
  #define DREAD(x) FastGPIO::Pin<x>::isInputHigh()
#endif

#ifndef TEST
  #include <SPI.h>
  #include <Wire.h>
  #ifdef LCD
    #include <LiquidCrystal_I2C.h>
    LiquidCrystal_I2C lcd(0x27, 20, 4);
    long lcdHash = 0;
  #else
    #include <Adafruit_SSD1306.h>
    Adafruit_SSD1306 display(128, 64, &Wire, -1);
  #endif
#endif

#include <EEPROM.h>

unsigned long buttonTime = 0;
long loopCounter = 0;
bool isOn = false;
unsigned long resetMillis = 0;
bool resetOnStartup = false;

int hmmpr = 0; // hundredth of a mm per rotation
int savedHmmpr = 0; // hmmpr saved in EEPROM
int hmmprPrevious = 0;

long pos = 0; // relative position of the stepper motor, in steps
long savedPos = 0; // value saved in EEPROM

long leftStop = 0; // left stop value of pos
long savedLeftStop = 0; // value saved in EEPROM
bool leftStopFlag = true; // prevent toggling the stop while button is pressed.

long rightStop = 0; // right stop value of pos
long savedRightStop = 0; // value saved in EEPROM
bool rightStopFlag = true; // prevent toggling the stop while button is pressed.

volatile unsigned long spindleDeltaTime = 0; // millis() of the previous spindle update
volatile int spindleDeltaPrev = 0; // Previously detected spindle direction
volatile long spindlePos = 0; // Spindle position
long savedSpindlePos = 0; // spindlePos value saved in EEPROM
long spindleLeftStop = 0;
long spindleRightStop = 0;

volatile int spindlePosSync = 0;
int savedSpindlePosSync = 0;

int stepDelayUs = PULSE_MAX_US;
bool stepDelayDirection = true; // To reset stepDelayUs when direction changes.
unsigned long stepStartMs = 0;

bool showAngle = false; // Whether to show 0-359 spindle angle on screen
bool savedShowAngle = false; // showAngle value saved in EEPROM
bool showAngleFlag = true;
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

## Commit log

2025-06-29 rewire encoder knob to ESP
2025-10-22 added encoder
2025-10-26 fixes/adaptation to my lathe
    [config.h, h5.ino]
2026-02-17 added ADC1115
    [EncoderMount38.4mm-Body.step, EncoderMount38.4mm-Wheel.step, h5case.step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]
2026-02-17 Fixed line endings
    [h5case.step, h5handle.step, h5mount1.step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]
